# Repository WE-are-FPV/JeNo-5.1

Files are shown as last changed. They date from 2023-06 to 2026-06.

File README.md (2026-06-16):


> [!NOTE]
> Current version : **1.6.0** (read [changelog](#changelog) for details)

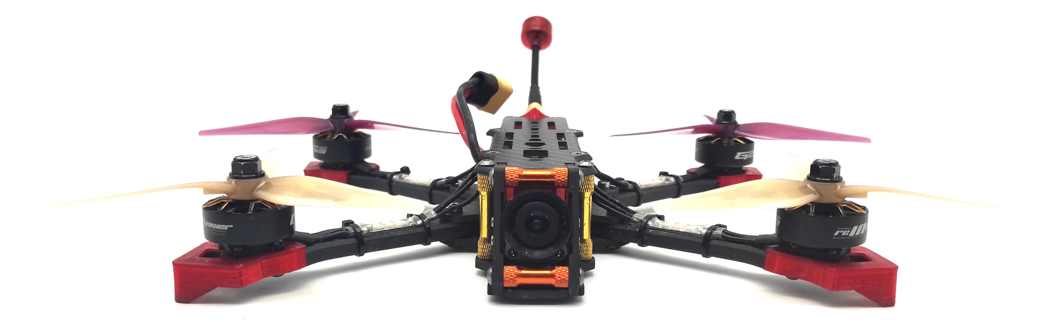
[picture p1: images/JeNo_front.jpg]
JeNo - Front view


# JeNo 5.1"
***5.1" drone FPV frame compatible with Air Unit O3 and O4 Pro, designed for Freestyle, Freeride and Cinematic. Many customizable options are available.***

> [!NOTE]
> Designed in France by members of the [WE are FPV](https://www.wearefpv.fr/) community, the JeNo is already flown by hundreds of pilots and is now being sold by [Drone FPV Racer](https://www.drone-fpv-racer.com/recherche?controller=search&s=JeNo+5.1+frame&aff=64&id_campaign=13) (affiliate link). The French version of the project is available on [Printables](https://www.printables.com/fr/model/339099-jeno-51-drone-frame). Note that a [2.5" version](https://github.com/WE-are-FPV/JeNo-Pocket), [3-3.5" version](https://github.com/WE-are-FPV/JeNo-3-3.5) and a [7-8" version](https://github.com/WE-are-FPV/JeNo-7) of the JeNo exist.

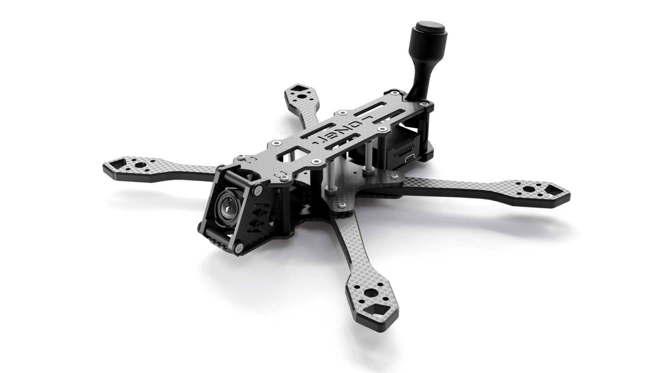
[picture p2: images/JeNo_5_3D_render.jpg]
JeNo classic - 3D render


## Table of contents

* [Key features](#key-features)
* [Presentation](#presentation)
* [Detailed specifications](#detailed-specifications)
* [Versions and files](#versions-and-files)
* [Customization](#customization)
* [Buy it or cut it !](#buy-it-or-cut-it-)
* [Bill of materials](#bill-of-materials)
* [Building/Assembly guide](#buildingassembly-guide)
* [Inspiration](#inspiration)
* [Tuning, Betaflight Preset](#tuning-betaflight-preset)
* [Blackbox](#blackbox)
* [Videos](#videos)
* [Builds examples](#builds-examples)
* [Authors](#authors)
* [TPU](#tpu)
* [Community (remixes and TPU)](#community-remixes-and-tpu)
* [Changelog](#changelog)

## Key features
- [x] **Sturdiness** and **rigidity** (6 mm arms)
- [x] Excellent flight **performances**, easy to tune
- [x] **Wide-X** geometry
- [x] Perfect DJI **Air Unit O3 O4 Pro** camera integration
- [x] Designed for : DJI Vista/AU O3/AU O4 Pro, WalkSnail, HDZero, Analogic
- [x] **Frame and standoffs NOT visible** in video feed, with any FPV camera
- [x] Stack **decoupled** from the arms
- [x] **Easy maintenance** : remove 2 screws to replace an arm
- [x] **Roomy** (30 mm high)
- [x] **Customizable** (weight, arms, camera plates)

## Presentation
The **JeNo** is a 5.1" frame designed for the **DJI Air Unit O3**, which is not compatible with most of existing frames. It was designed to ensure that the frame is not visible in the camera's field of view (FOV) while providing good lens protection. It is also compatible with the O3 camera's ND filters.

The JeNo is now compatible with the **JI Air Unit O4 Pro** (but make sure to use vertical ND filters, like [those from GEPRC](https://geprc.com/product/geprc-dji-o4-air-unit-pro-filter/)).

Originally intended for freestyle flying, **flight quality** and **durability** were at the core of its design (see BlackBox at the bottom of the page).

The issue of obstructed FOV due to standoffs or the frame itself is exacerbated with the O3/O4 Pro camera, but this issue already exists in many frames with other cameras. The JeNo allows for a clear FOV **with any camera** and is **not exclusively dedicated to the O3/O4 Pro**.

It is optimized for a 25° camera tilt but can support FOVs ranging from 0° to ~40°. A high tilt option is also available.

This new ability to film in **4K without needing an Action Cam** saves between 70g (Action 2) and 165g (GoPro 11) (plus TPU). For the standard version of the JeNo, we decided to add 20g to the frame to have a **rigid and sturdy tank**, totaling up to **~140g**. However, it still allows for the option of carrying an Action Cam.

A set of **[optimized TPU for bando bashing](https://github.com/WE-are-FPV/JeNo-5.1/tree/main/tpu/bando_edition)** is also available to guarantee the best durability.

With a DJI Air Unit O3/O4 Pro, you benefit from a **lighter and more robust** setup compared to traditional frames, with a clear FOV.

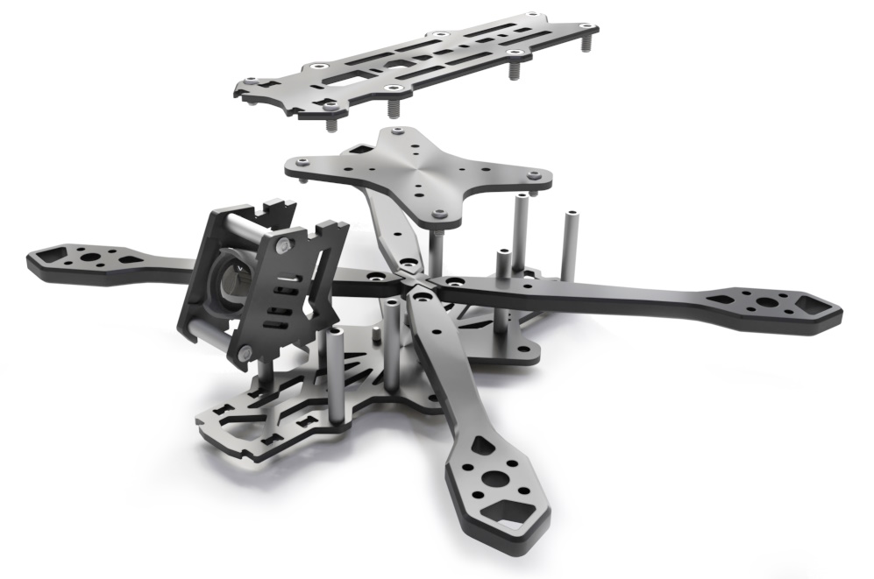
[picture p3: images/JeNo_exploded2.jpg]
JeNo - exploded view


A **Light version** will allow you to maintain a more typical weight around **120g**.

The JeNo was initially designed for Freestyle flying, which is why it features a "Wide-X" geometry. This design allows for good handling while reducing the amount of **visible propellers in the FOV** compared to a "True-X" frame (though some propellers may still be visible). A **"Cinematic" option** provides **elongated camera plates** for a **"Wide" FOV without visible propellers**.

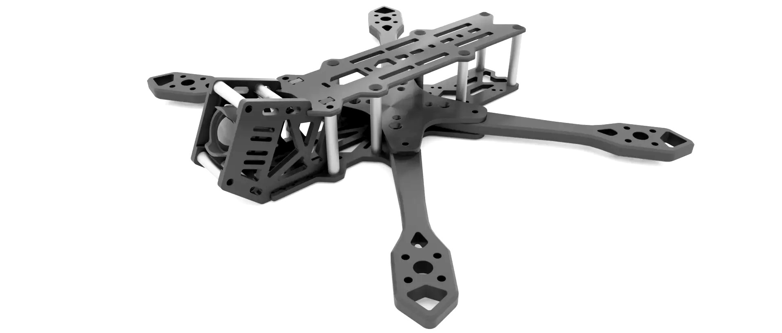
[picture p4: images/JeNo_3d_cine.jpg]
JeNo Cinematic - 3D render


Several pattern options for the arm are also available.

Finally, as this frame was designed by members of the [WE are FPV](https://www.wearefpv.fr/) community, a "WaF edition" is available (the logo is engraved on the bottom plate, you can remove it if you prefer). Join us on the WAF forum in [the official JeNo 5.1" thread](https://forum.wearefpv.fr/topic/19574-jeno-51-un-ch%C3%A2ssis-custom-modulaire-avec-fov-d%C3%A9gag%C3%A9-o3) to discuss it further.

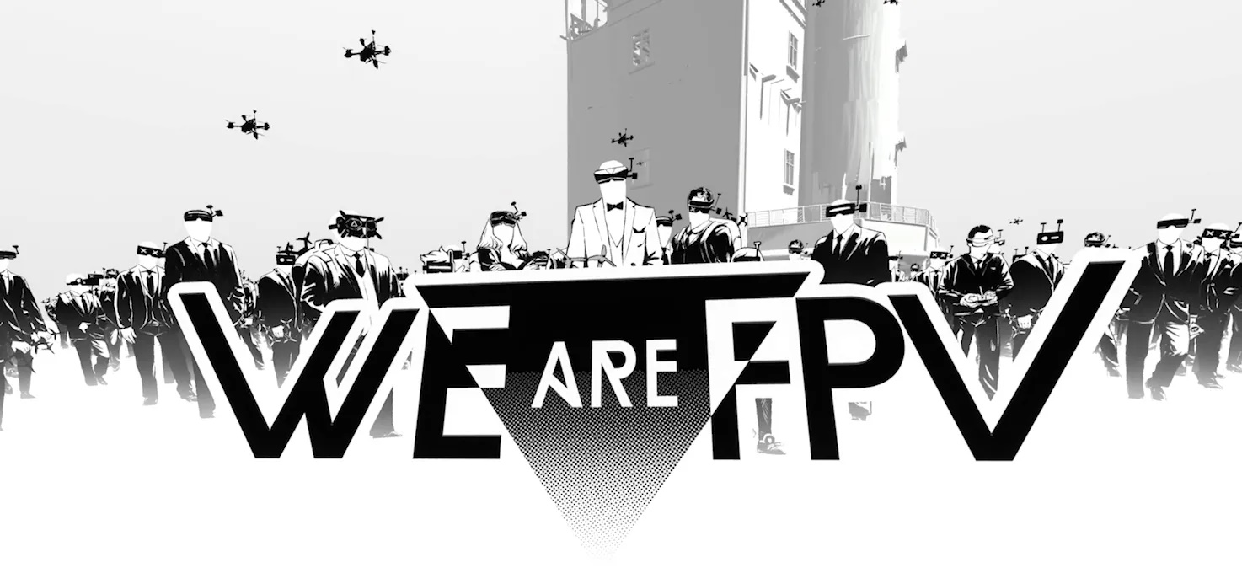
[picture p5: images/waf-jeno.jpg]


The JeNo is also available in [2.5" version](https://github.com/WE-are-FPV/JeNo-Pocket), [3" and 3.5" versions](https://github.com/WE-are-FPV/JeNo-3-3.5) and [7" and 8" version](https://github.com/WE-are-FPV/JeNo-7).

## Detailed specifications

||| 
| :--- | :--- |
| **Geometry** | Wide-X | 
| **Props size** | 5.1" (or 6" with optional arms) | 
| **Weight** | 120 to 145 g depending on options, with screws | 
| **Arms** | 6 mm | 
| **Body height** | 30 mm | 
| **Stack height** | 21.5 mm | 
| **Bottom plate** | 2.5 or 3 mm depending on options | 
| **Middle plate** | 2.5 mm | 
| **Top plate** | 2 mm | 
| **Camera plates** | 3 mm | 
| **Motors mounting** | 16 mm | 
| **Camera** | 20 mm (DJI), Micro, Nano. Clear FOV. Ajustable.
| **Main stack** | 30.5 mm x 30.5 mm and 20 mm x 20 mm | 
| **Back stack** | 20 mm x 20 mm and 25 .5 x 25.5 mm | 
| **Supported VTX** | Analogic, DJI Vista, DJI Air Unit O3/O4 Pro, WalkSnail, HDZero… | 
| **Strap passage** | Yes | 
| **XT60 passage** | Yes (front and back) + passage for a zip tie | 

## Versions and files

### Frame versioning
You will find the **current version** of the frame at the beginning of the description and the full [history of modifications](#changelog) at the end of the page.

We strongly recommend always cutting the latest version to ensure you benefit from the most recent optimizations.

The version **number format** is as follows :
```
<Major versions>.<Minor version>.<Revision>
ex : 1.3.2
```

* **Revision :** This number is incremented in the case of minor modifications with no significant impact.
* **Minor version :** This number is incremented for minor modifications that may potentially break compatibility with certain TPU parts.
* **Major version :** This number is incremented for significant modifications that break compatibility at the carbon level.

Since the creation of the JeNo 5", we have always strived to **maintain compatibility at the carbon level**. As a result, the version remains “1.x.y.”

In practical terms, this means that if you have the very first version of the JeNo 5" and want to equip it with the **O4 Pro**, you only need to have new camera plates cut—they will be compatible with your frame version!

### TPU Versioning

Since TPU parts are tied to the **frame version**, as explained in the previous section, TPU **names are prefixed** with chassis version **compatibility information**, for example :

* JeNo5_**1.6** : compatible with version **1.6**
* JeNo5_**1.x** : compatible with **all** versions
* JeNo5_**1.5+** : compatible starting from version **1.5**

**Note :** if you are developing TPU parts for the JeNo, make sure to clearly indicate which frame version they are compatible with.

### Files management
To simplify things, we have reorganized the file structure. The files are now divided into **five groups** :

* **01-FRAME :** Contains **models** describing the **frame** in DXF, STEP, and STL formats for the current version. Also contains a PDF file which is a reformatted version of the DXF.
* **02-TPU :** Contains **TPU models** for the current frame version in STL format.
* **03-FRAME-HISTORY :** Contains previous versions of the frame.
* **04-TPU-HISTORY :** Contains TPU models that are no longer compatible with the current version.
* **OTHER-FILES :** Contains documentation files, including the assembly manual and a description.

The major change is that all options are now consolidated into a single file. This will make version management significantly easier for us.

If you want to view the DXF file with all annotations, we recommend using the free software [DWG TrueView](https://www.autodesk.com/products/dwg-trueview/overview). If you prefer not to use it, the PDF version of the file will contain all the necessary information.

## Customization

The JeNo is customizable, offering several **options** to best adapt to different needs and individual preferences.

To have a complete frame, you will need to choose:

* A **base** (bottom, middle, top plate, and arm spacer)
* A type of **camera plates**
* A model of **arms**

> [!TIP]
> All components are compatible with each other.

Here is a preview of the "menu card" and its various options:

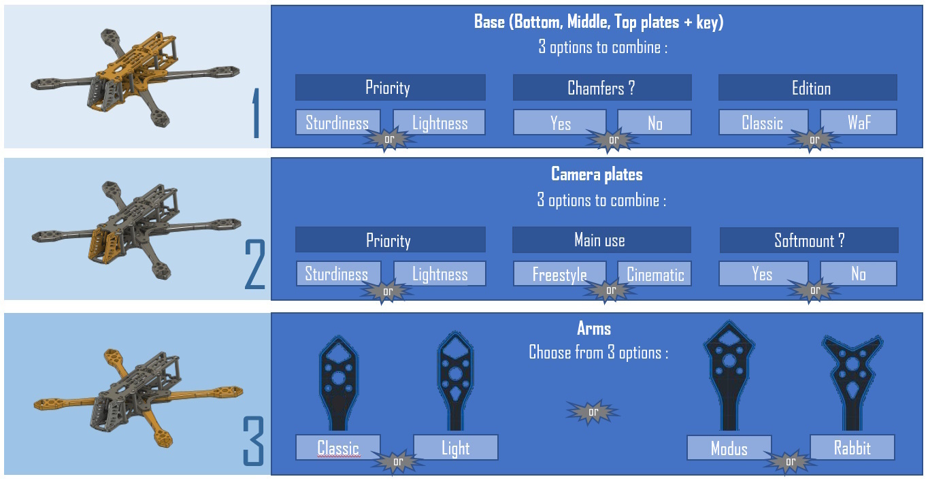
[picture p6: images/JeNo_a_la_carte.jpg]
JeNo customizable options


### The Base
This concerns the core of the frame (bottom, middle, top plates, and arms key).

* **Priority :** The Classic version (sturdy) features a 2.5mm bottom plate, compared to 2mm for the Lightweight version, which is also more "patterned." For the Lightweight version, the weight is approximately 120g depending on the options, compared to approximately 140g for the reinforced (classic) version.
* **Chamfers :** Chamfers have been removed from the files as they are not used by carbon cutters. We recommend applying chamfers to the entire frame, except for the camera plates, for aesthetics, comfort, and durability. Chamfering generally increases the price by around 15%.
* **Edition :** The WE are FPV option adds a "WaF" logo engraved under the bottom plate. You are free to have it removed during cutting or replaced with another design.
* **Bando :** t is the most robust option, with a 3mm thick bottom plate and reinforced arms.

### The Camera Plates

_**Priority :** In the Lightweight version, the carbon is more "patterned," making it slightly more fragile._

* **Classic :** For Freestyle flying, behavior and robustness are prioritized, but the **propellers will be visible in the FOV**.
* **Lightweight :** 2.7g lighter than the Classic plates (1.35g per plate).
* **Cine :** Uses elongated camera plates to remove propellers from the FOV (set to Wide with the O3).
* **Ciné Soft :** The version without soft mounting allows for more adjustment of the camera position. In the case of using the Air Unit O3, the quad must be properly tuned to avoid vibrations in video recording. The soft mounting version limits vibrations that could reach the camera. However we had no vibration with hard mounted O3.
* **High tilt :** allows for a 40° tilt for high tilt adepts
* _**Variable tilt :** variation proposed on [Kamarad70's Thingiverse page](https://www.thingiverse.com/kamarad70/designs)_

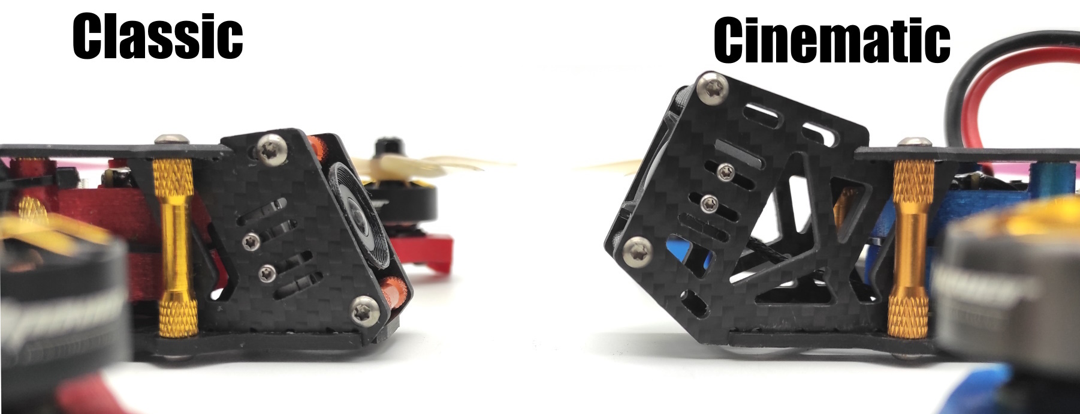
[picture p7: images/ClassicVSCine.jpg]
JeNo Classic vs Cinematic


> [!CAUTION]
> Note: The coaxial cable sold with the Air Unit O3 (11.5 cm) barely fits with the cinematic camera plates. It is recommended to use a 20 cm coaxial cable (sold by RunCam and AxisFlying).
>
> Air Unit O4 Pro coaxial cable is long enough.

| Freestyle camera plates | Cinematic camera plates |
| :---: | :---: |
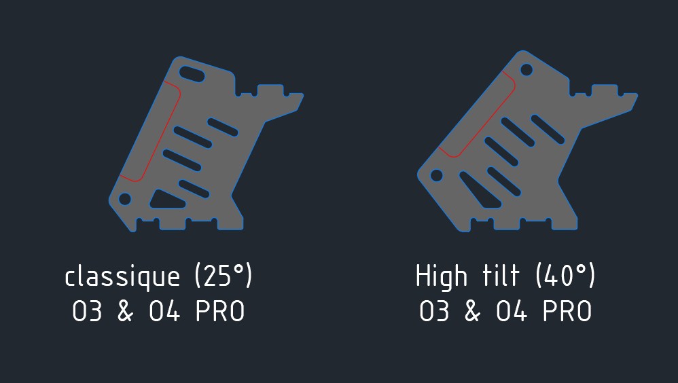
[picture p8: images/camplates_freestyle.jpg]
Freestyle camera plates
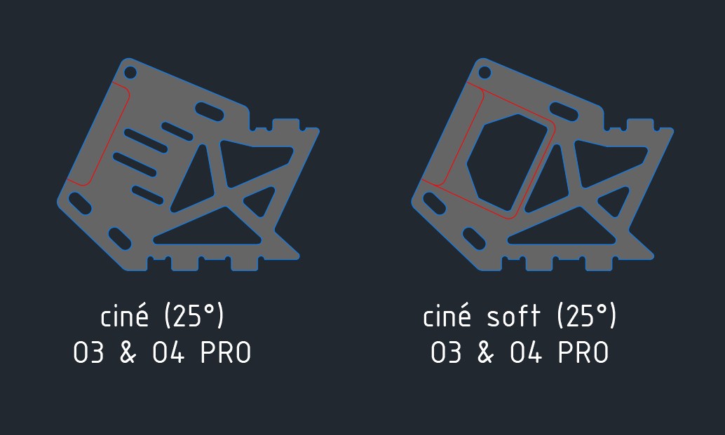
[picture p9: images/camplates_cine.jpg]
Cinematic camera plates
|  |  |
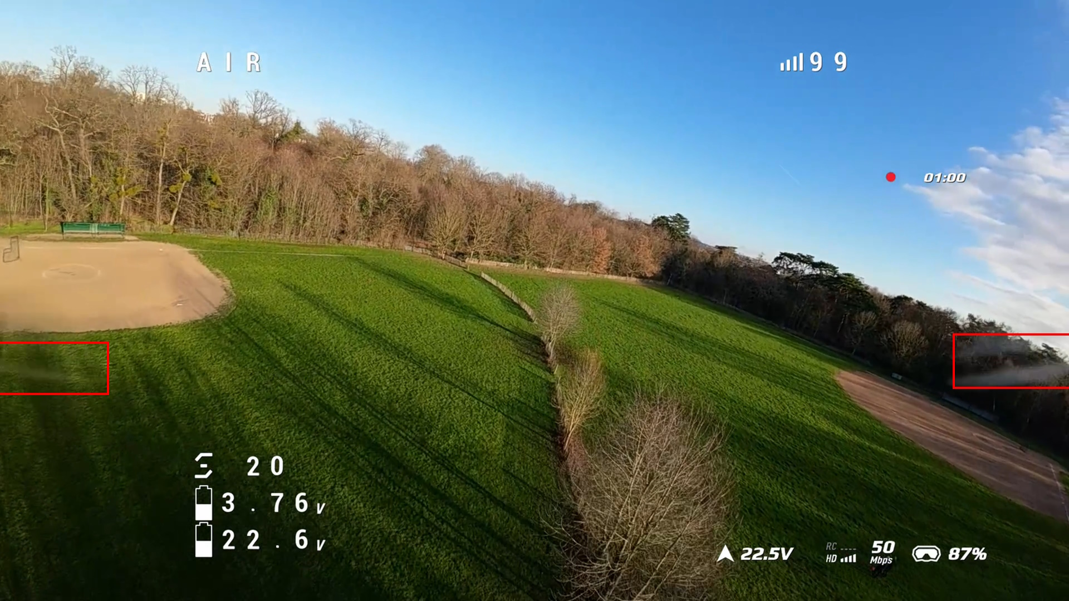
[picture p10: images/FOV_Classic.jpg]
Freestyle Props in FOV
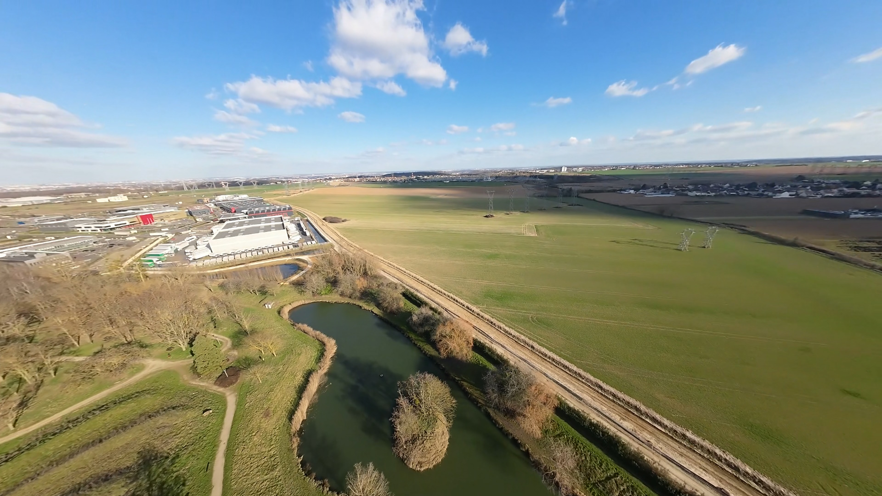
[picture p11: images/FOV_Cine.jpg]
Cinematic No Props in FOV
|  Props in view |  NO props in view |

### The Arms
Several shapes are available for the arm. Weight, robustness, motor protection, and aesthetics will be the main considerations.

* **"Classic" :** A solid design suitable for Freestyle flying.
* **"Light" :** Some solidity is traded in favor of reduced weight.
* **"Modus" :** The most robust shape that offers the best motor protection. It is also the heaviest arm model.
* **"Rabbit" :** Provides good motor protection with a reasonable weight.
* **"Bando Edition" :** A beefier and stronger model

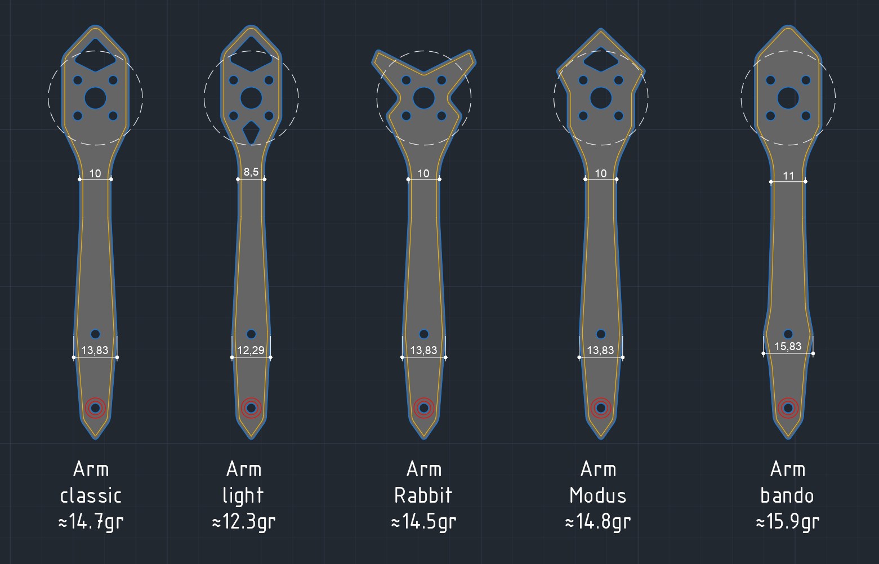
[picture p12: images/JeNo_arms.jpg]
JeNo Arms


### The Extras
In the DXF file, you will find additional options. These "extras" cater to more specific needs but remain compatible with the JeNo :

* 6" Arms
* Ultra-light Camera Plates
* High Tilt Camera Plates (40°)
* Top plate with 2 or 3 straps areas
* ...

Feel free to modify the files according to your requirements as well. For example, if you want even more solidity, you can indicate that you would like thicker bottom and top plates (remember to adjust the screw length accordingly).

A 3mm bottom plate for use in bando is an interesting optimization and does not affect the screws length.

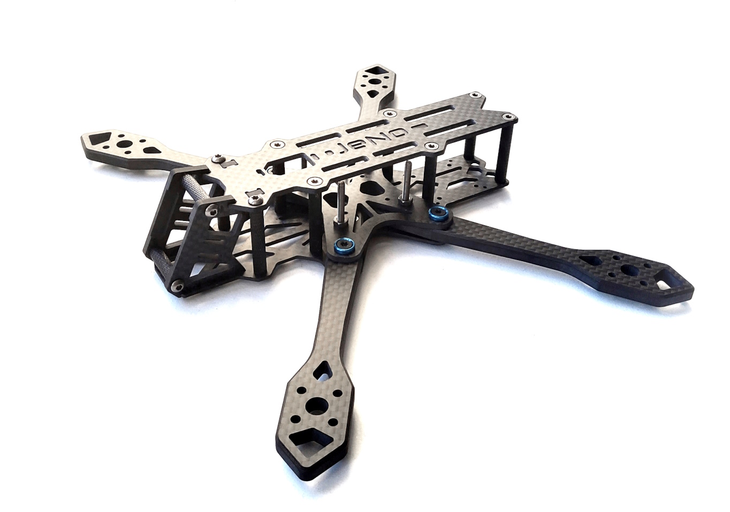
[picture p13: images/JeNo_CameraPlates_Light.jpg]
||
|:---:|
| Classic Base Light + Light Camera Plates + Classic Arms |

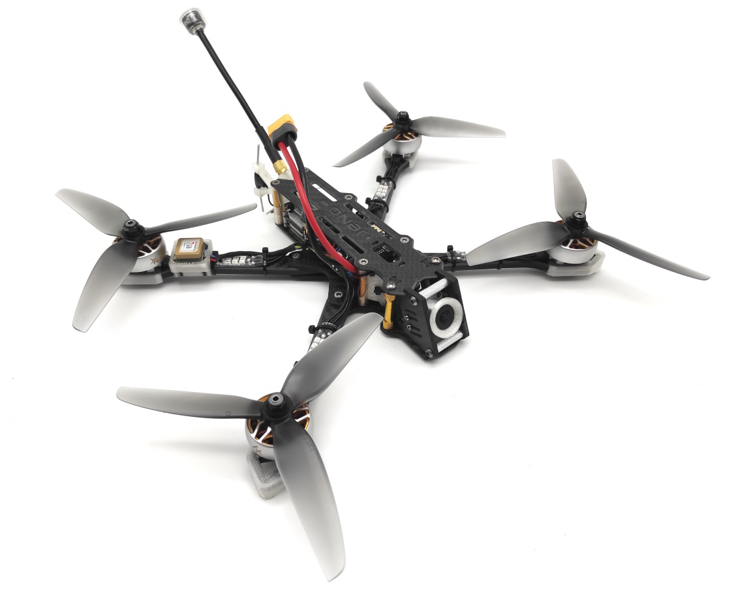
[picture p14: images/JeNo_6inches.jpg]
||
|:---:|
| JeNo Classic + 6" Arms |

## Buy it or cut it !

It is up to you : you can get it cut or you can get a classic or cine version directly from Drone FPV Racer or La Camera Embarquée :

* [JeNo Classic by DFR](https://waf.link/JeNo-DFR) (affiliate link)
* [JeNo Cine by DFR](https://waf.link/JeNo-Cine-DFR) (affiliate link)
* [JeNo Classic by La Caméra Embarquée](https://www.lacameraembarquee.fr/we-are-fpv/17793-chassis-we-are-fpv-jeno-51-classic.html) (affiliate link)
* [JeNo Cine by La Caméra Embarquée](https://www.lacameraembarquee.fr/we-are-fpv/17789-chassis-we-are-fpv-jeno-51-cine.html) (affiliate link)
* [FPV CNC Drone](https://fpvcncdrone.com/)

Note: Prices are often excellent in stores, but they don’t always offer the latest version.

The JeNo 5.1" is also available from [CNC Madness](https://cncdrones.com/jeno-5-classic.html) (Canada).

Of course, you can directly contact your favourite carbon fiber cutting service.

The ["01-FRAME"](https://github.com/WE-are-FPV/JeNo-5.1/tree/main/01-FRAME) folder contains all the files you need to get it **cut** in your favourite flavour.

Consult the **DXF file** of the frame (or the PDF version) to choose the version that interests you.

Feel free to select a pre-made "Edition" (Classic, Light, or Bando), or mix different options and choose certain "extras".

You will also need to choose a type of camera plates (classic, cine, etc.).

> [!NOTE]
> All parts versions are compatible with each others

## Bill of materials

In addition to the carbon fiber, you will need the following hardware to complete the assembly of the frame.

**Standoffs**

It is recommended to use 5mm diameter standoffs, especially for those that will serve as support for TPU (backpack and capacitor). Moletted spacers can still be used, but the TPU supports will need to be modified accordingly.

| Quantity | Description | Details |
| :---: | :--- | :--- |
| 8 | M3x30mm standoffs | for the body |
| 2 | M3x20mm standoffs | for the camera |

**Stack materials**

* If 30x30 stack

| Quantity | Description | Details |
| :---: | :--- | :--- |
| 4 | M3x22mm ou M3x20mm countersunk screws | for the stack |
| 4 | M3 nuts for stack screws | |

* If 20x20 stack

| Quantity | Description | Details |
| :---: | :--- | :--- |
| 4 | M2x20mm countersunk screws | for the stack |
| 4 | M2 nuts for stack screws | |

**Frame materials**

| Quantity | Description | Details |
| :---: | :--- | :--- |
| 6 | M3x6/8mm countersunk screws | for the top plate |
| 14 | M3x8mm screws (titanium if possible) | for the bottom and camera plates |
| 8 | Pressnuts ([Flywoo](https://www.drone-fpv-racer.com/flywoo-m3-clinch-nuts-20-pcs-7965.html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) or SourceOne alike) | |
| 4 | M3x14mm screws (steel if possible) | for the arms |
| 4 | M3x8mm screws (steel if possible) | for the arms |

**Additional materials**

| Quantity | Description | Details |
| :---: | :--- | :--- |
| 16 | M3x10mm screws (if using arms protections) or M3x8mm (if no TPU) | for the motors |
| 4 | M2x5mm screws | for the camera |

_**In the absence of arm protection, 8mm screws are recommended. 10mm screws are sometimes too long for certain motors and can cause current leaks.**_

**Fasten the lipo**

The JeNo allows the use of non-slip straps thanks to its strap slots. You can also use a LiPo pad if desired.

## Building/Assembly guide

Find numerous examples of builds on the _**DroneBuilds**_ page of WE are FPV.
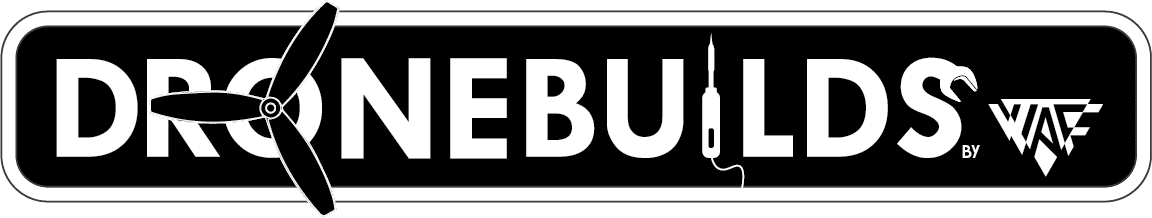
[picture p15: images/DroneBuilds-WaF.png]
DroneBuilds (https://forum.wearefpv.fr/71-dronebuilds/ "DroneBuilds - Click to Access!")


The assembly of the frame is straightforward, but here are some clarifications:

* On one of the two sides of the middle plate, there are chamfered holes to accommodate countersunk screws. This side corresponds to the bottom. Remember to install the stack screws before installing the middle plate.
* The press nuts will be positioned on the bottom side of the bottom plate.
* An RX antenna in the shape of a T can be attached to the back of the JeNo using zip ties.
* Six screws on the top plate are countersunk screws to avoid damaging the LiPo battery.

Here is a [video of the JeNo assembly (FR)](https://youtu.be/SF4UAqyNPJ0), and you will find the assembly documentation below, also available here in [PDF format](./OTHER-FILES/JeNo5_Assembly_Guide.pdf).

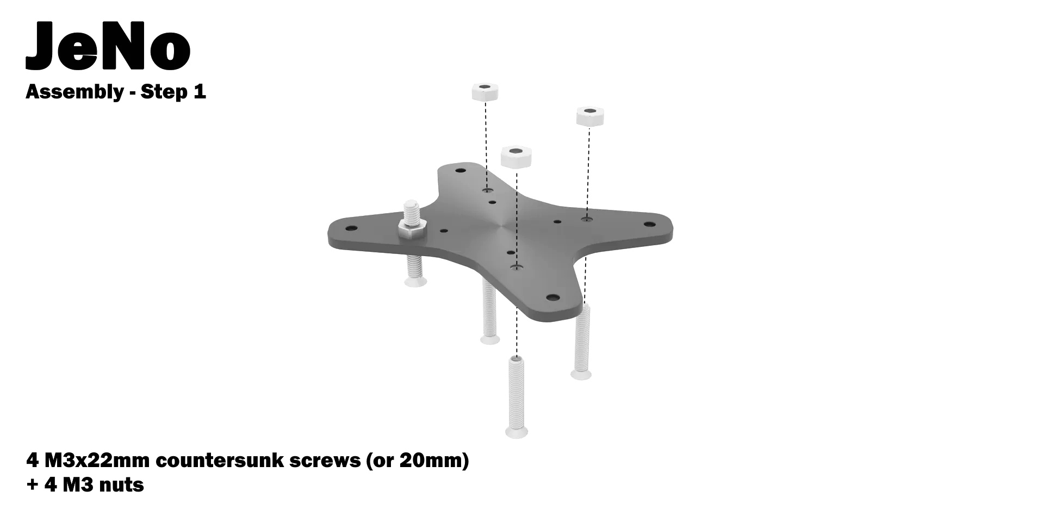
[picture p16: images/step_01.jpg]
JeNo assembly - step 1

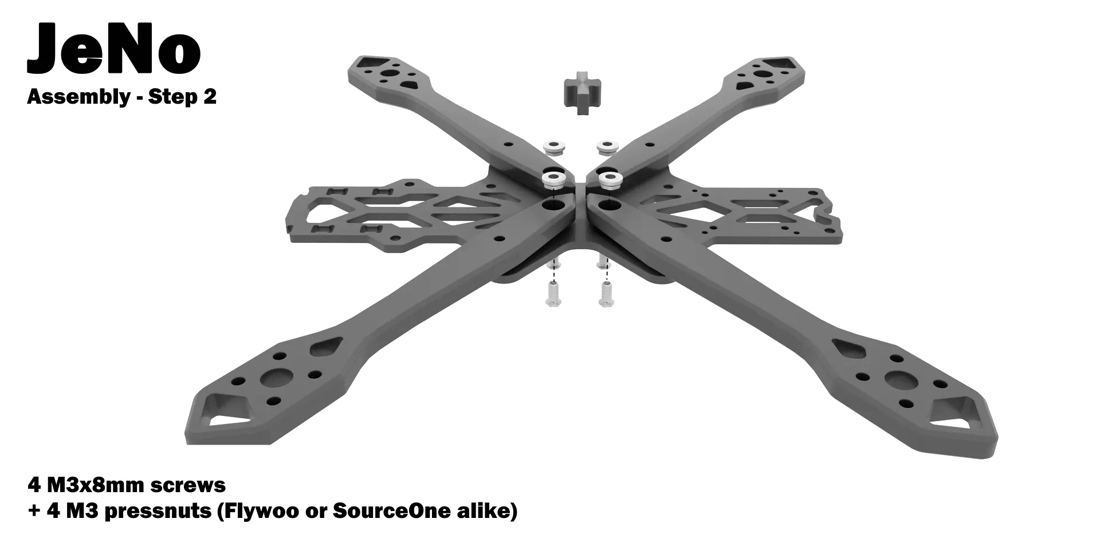
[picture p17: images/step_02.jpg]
JeNo assembly - step 2

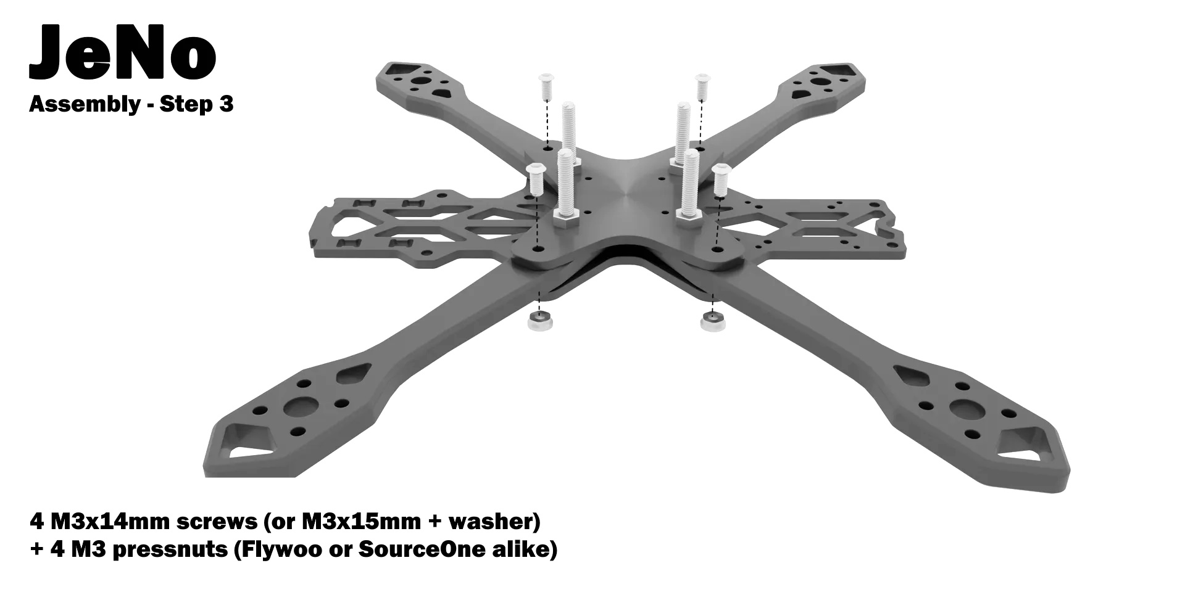
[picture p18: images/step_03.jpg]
JeNo assembly - step 3

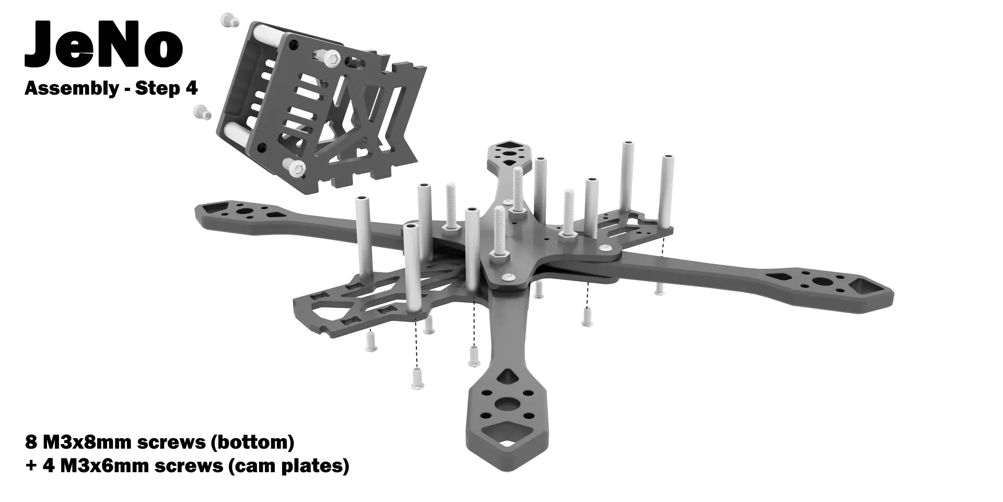
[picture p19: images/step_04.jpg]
JeNo assembly - step 4


The assembly is illustrated with cinematic camera plates, which allow the use of up to 4 standoffs (see visual in step 5 below). In practice, 2 standoffs at the front are sufficient, just like with regular camera plates (see step 4).

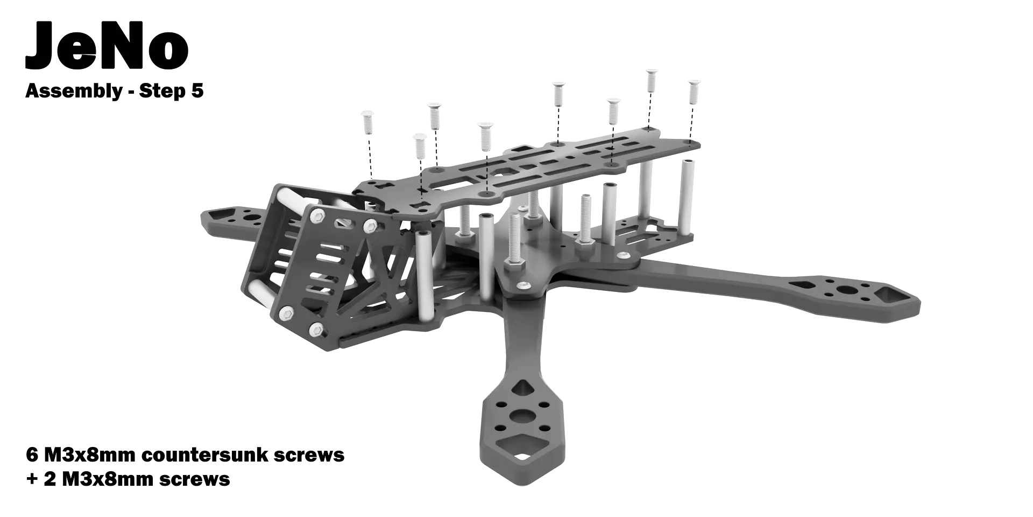
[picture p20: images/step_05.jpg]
JeNo assembly - step 5

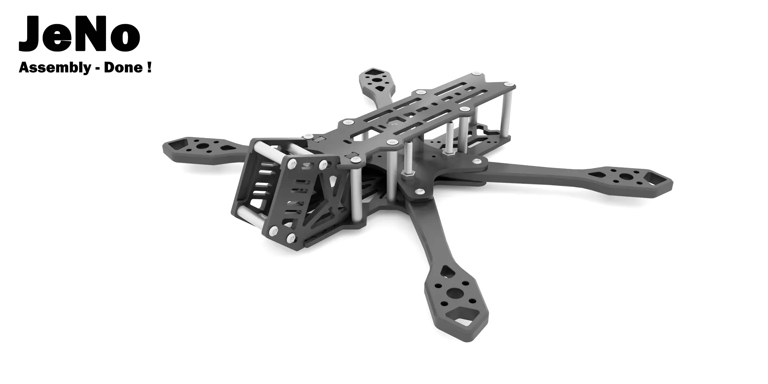
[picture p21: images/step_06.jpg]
JeNo assembly - step 6


## Inspiration

The JeNo takes partial inspiration from two other frames:

* The arm locking system of the **Apex**, with **embedded press nuts** at the end of the arms.
* The camera plates are slightly inspired by the **aluminum** cage of the **iFlight Evoque F5X HD V2**. The design is completely different as we use only carbon fiber, but the look is similar.

The rest of the design was guided by the constraints imposed by the Air Unit O3 and its camera, as well as our past experiences with other custom frame designs.

## Tuning, Betaflight Preset

To quickly and fully enjoy the JeNo, a **preset** for **Betaflight 4.4 and 4.5** is available. You just need to add the **WE are FPV repository** to the **preset sources** in Betaflight Configurator.

In the "Preset" tab, click on "Preset sources..." to add the WE are FPV source:

- **Url :** https://github.com/WE-are-FPV/firmware-presets
- **GitHub branch :** waf-presets

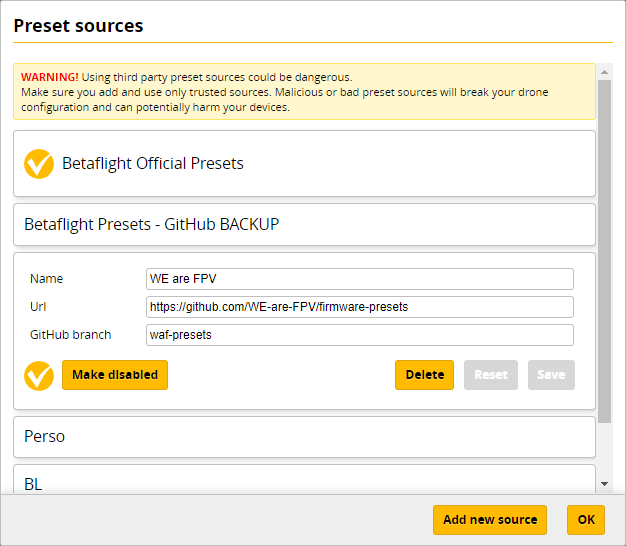
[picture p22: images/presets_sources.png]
JeNo Preset Source


Once the source is validated, you simply need to make it "active" to access the JeNo presets under the **"Tune" category** in **version "4.4 or 4.5"**. The preset is available in both **French (FR)** and **English**, and it is indeed the **same tune**.

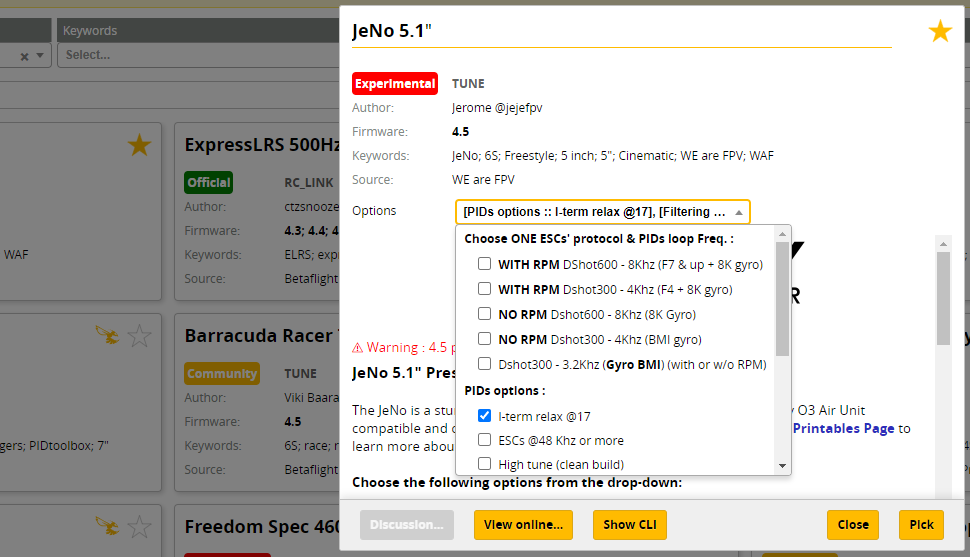
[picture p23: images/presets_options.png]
JeNo Preset Options


The preset contains **several options** to select. Note that **by default**, the **tune** is already **quite aggressive**, even without activating the "advanced" tuning options for PIDs and filtering.

## Blackbox

Here is an overview of vibration distribution on the 3 axes for the JeNo "classic Freestyle." This is indeed the unfiltered gyro signal for a 3 minutes freestyle flight :

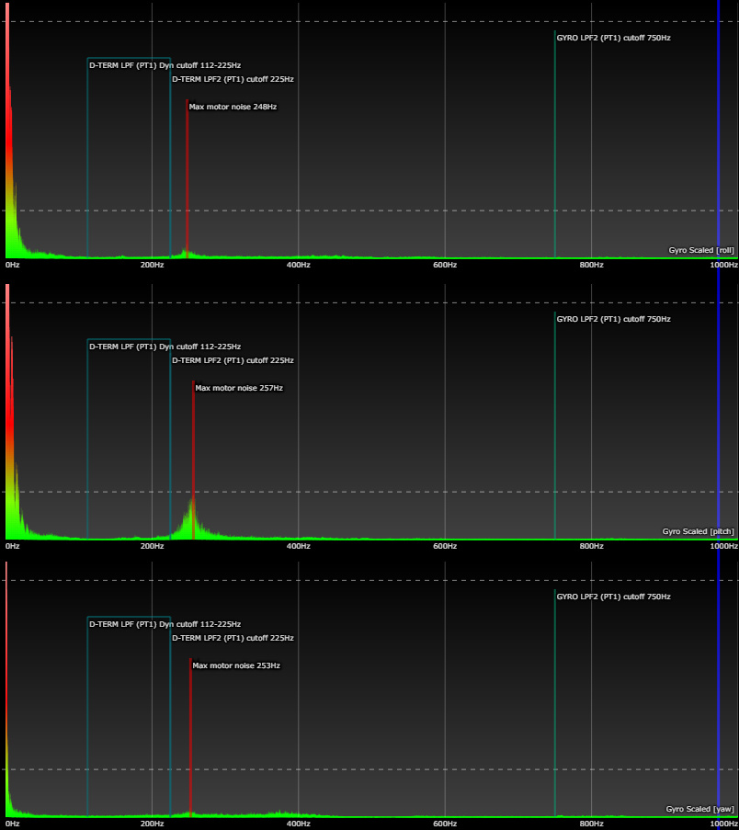
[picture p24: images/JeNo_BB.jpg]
JeNo Blackbox


## Videos
Freestyle with JeNo :

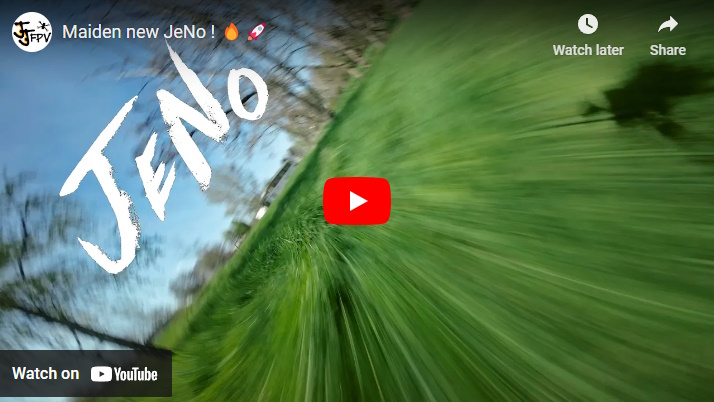
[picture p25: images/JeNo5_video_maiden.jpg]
JeNo 5.1 Maiden (https://www.youtube.com/watch?v=Fe3_sJf0j6o "JeNo 5.1 Maiden - Click to Watch!")


JeNo review on WE are FPV (French) :

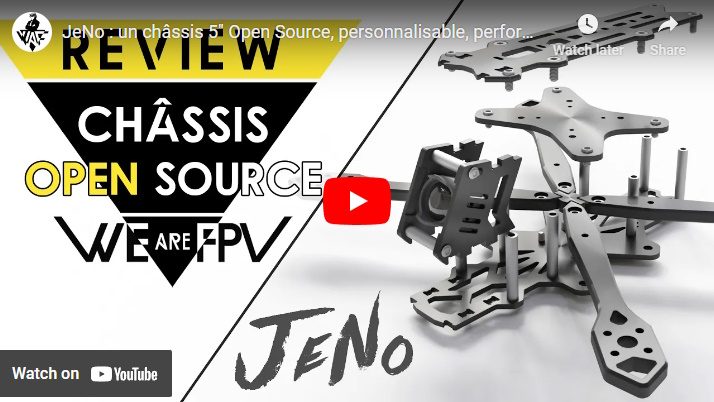
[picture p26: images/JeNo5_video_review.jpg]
JeNo review on WE are FPV (French) (https://www.youtube.com/watch?v=RtPTJsno8Kg "JeNo review on WE are FPV (French) - Click to Watch!")


## Builds examples

You can find many build examples on [WE are FPV's DroneBuilds](https://forum.wearefpv.fr/71-dronebuilds/) and [RotorBuilds](https://rotorbuilds.com) :

* en : [JeNo 5.1" WE are FPV O3](https://rotorbuilds.com/build/31216)
* fr : [Iron JeNo 5.1" (Vista)](https://forum.wearefpv.fr/topic/20347-iron-jeno-51-vista/)
* fr : [JeNo - DJI Air Unit O3 (5" 6S)](https://forum.wearefpv.fr/topic/19543-jeno-dji-air-unit-o3-5-6s/)
* fr : [JeNo 6" cine/midrange](https://forum.wearefpv.fr/topic/20536-jeno-6-cinemidrange/)
* fr : [JeNo 5.1" Hybride](https://forum.wearefpv.fr/topic/20239-jeno-51-hybride/)
* fr : [JeNo 5" Cam Plate Ciné](https://forum.wearefpv.fr/topic/19995-jeno-5-cam-plate-cin%C3%A9)
* ...

## Authors

The JeNo was designed by :

* nochamo - [Youtube](https://www.youtube.com/user/nochamo)
* Jerome / Jéjé FPV - [Youtube](https://www.youtube.com/@jejefpv)
* MotardGeek - [Youtube](https://www.youtube.com/@MotardgeekFr91) (requester and tester for Light version)

## TPU

Among the downloadable files, you will find a variety of TPU to protect your JeNo and different Action Cams.

Even more interestingly, in collaboration with **Alex**, also known as [Heim FPV](https://www.youtube.com/@heim_fpv589), from the **__#bandolovers__** team, we have designed a set of [TPU parts optimized for bando flying](https://github.com/WE-are-FPV/JeNo-5.1/tree/main/tpu/bando_edition). If you're looking to reinforce your JeNo to the maximum extent, this kit is tailored for you. It includes:

* A **front bumper** that will safeguard the entire camera cage and assist in absorbing frontal impacts. It is available for classic, cine and high tilt camera plates.
* A **back bumper** for worry-free matty flips (it also allows for attaching the RX antenna).
* A much sturdier and encompassing **VTX antenna support**, with an inclination that better tolerates impacts from the rear (available in O3 and "cherry" versions). 2 holes allow for an easy antenna ejection if required.
* 2 new **arm protections**, offering not only better arm protection but also motor protection. The first version is "clippable" and replaceable without disassembling the motors. The second completely encases the arm tips and has no chance of being ejected during a crash.
* An optimized **DJI Action 2 mount** for bando flying, without an ND filter, available in 20 and 25-degree versions (not the one on the photo here under, which is the classic version).
* A new **DJI Action 2 mount** remixed from [T4 Max FOV Action 2 DJI TPU Drone Mounts](https://www.printables.com/fr/model/217897-t4-max-fov-action-2-dji-tpu-drone-mounts) par [t4obrien](https://www.printables.com/fr/@t4obrien). It allows to secure the camera with a strap.

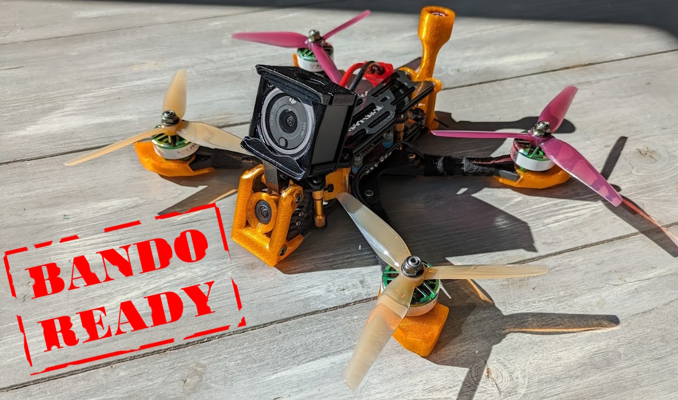
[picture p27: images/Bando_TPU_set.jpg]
Bando TPU set


If the cap of your Air Unit O3 antenna is lost, several designs are [available here](https://www.printables.com/fr/model/556697-dji-air-unit-o3-antenna-cap-3-versions) for replacement.

## Community (remixes and TPU)

**Fork/remix**
* [Platy FPV](https://www.youtube.com/channel/UCqOLDBE34WiqytAgCRManAg) has reimagined the JeNo to suit his needs: lighter, shorter, low profile, and with a split deck. Find all the details of the [JeNo 5.1" - PlatyStyle Edition](https://www.printables.com/fr/model/744619-jeno-51-platystyle-edition) on their Printables page and on the [WE are FPV forum](https://forum.wearefpv.fr/topic/22236-jeno-51-platystyle-un-jeno-sous-hormones).

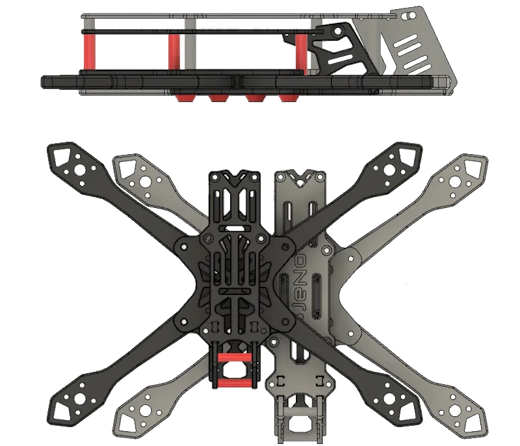
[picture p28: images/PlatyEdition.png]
PlatyStyle Edition


* [Kamarad70 (Rotor-Vision)](https://www.youtube.com/channel/UCQ9MUpBuCL820obqPXN7wsw) offers a variation of the JeNo camera plates on [his Thingiverse page](https://www.thingiverse.com/kamarad70/designs), allowing for an adjustable tilt (from -20° to approximately +40°). You will also find the associated [FPV camera mount](https://www.thingiverse.com/thing:6627268), a [front bumper](https://www.thingiverse.com/thing:6627192), and an [Action Cam support base](https://www.thingiverse.com/thing:6627160).

**TPU**

In addition to the TPU options available on this page, you will find here some TPU designs created by the community.

* [Pulse FPV](https://www.youtube.com/channel/UCUWnkQ2-IbQYc6LpTXz01qw) has created an impressive collection of high-quality TPU designs, which can be found on his [Thingiverse page](https://www.thingiverse.com/thing:5804682).

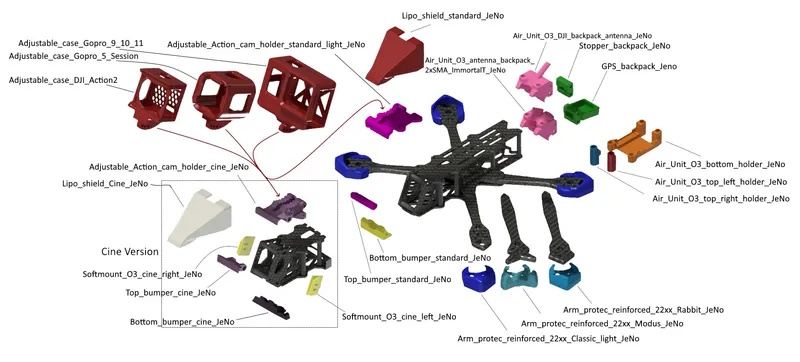
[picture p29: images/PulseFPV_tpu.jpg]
PulseFPV TPU


* [Bard FPV](https://www.youtube.com/@bardfpv) also offers us some interesting TPU designs on their [Cults3D page](https://cults3d.com/fr/collections-de-designs/BardFpv/jeno), including fins to protect the LiPo and facilitate the turtle mode.

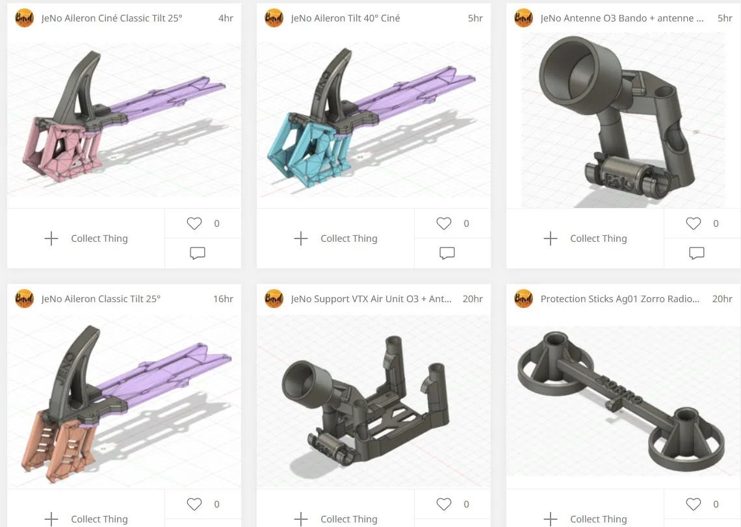
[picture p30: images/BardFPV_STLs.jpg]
Bard FPV STLs


* [Support GP9, Walksnail, GPS, ViFly etc.](https://www.thingiverse.com/-kc-/designs) by [kC](https://www.youtube.com/@kCer)
* [Modus rising arm protection](https://www.printables.com/fr/model/830201-jeno-51-protection-bras-modus) to safeguard the bells, [short double antenna backpack](https://www.printables.com/fr/model/830229-jeno-51-support-double-antennes-vista-pour-o3) by [Florian](https://www.printables.com/fr/@FloG_149541/models). 
* Several [GoPro mounts](https://www.printables.com/fr/@PhenXFrame/models) (5 to 7 and 9 to 12) by [Phen X Frame](https://www.printables.com/fr/@PhenXFrame)
* [GoPro Mini 11 mount](https://www.printables.com/fr/model/831787-jeno-51-gopro-11-mini-mount) and other STL files by [L4go](https://www.printables.com/fr/@L4go_1956352)
* [GoPro Mini 11 mount](https://www.printables.com/fr/model/590286-gopro-11-mini-pour-jeno-cine) for JeNo Cine by [shaks](https://www.printables.com/fr/@shaks_729955)
* [O3 case](https://www.printables.com/model/1032747-jeno-bando-o3-casing-ranxfpv), 2 O3 backpacks with fins ([V1](https://www.printables.com/model/976839-jeno-bando-o3-backpack-ranxfpv) and [V2](https://www.printables.com/model/1032734-jeno-bando-o3-backpack-ranxfpv-v2)) and a [front bumper with fins](https://www.printables.com/model/1032740-jeno-bando-bumper-avant-ranxfpv) by [Franck G](https://www.printables.com/@FranckG_2243891)
* Still by [Franck G](https://www.printables.com/@FranckG_2243891), but for the O4 Pro : DJI O4 Pro casing ([V1](https://www.printables.com/model/1144921-jeno-bando-dji-o4-pro-casing-ranxfpv), [V2](https://www.printables.com/model/1168238-jeno-bando-dji-o4-pro-casing-ranxfpv-v2)), [front bando bumper](https://www.printables.com/model/1158816-jeno-o4-pro-bando-bumper-avant-ranxfpv) and [a linear antennas backpack](https://www.printables.com/model/1146819-jeno-bando-dji-o4-o3-backpack-ranxfpv-v3)

## Changelog

> [!TIP]
> Compatibility is consistently maintained between each version: if your frame was a v1, the parts from v1.2 will be compatible. The same applies to TPU accessories. That's why we don't keep the history of previous versions.

* Version **1.6.0** (13/12/2025) :
  * New bottom plate for all variants : reinforcement of the front section around the camera plate slots
  * New top plate for all variants : widened carbon area around the rear holes to make cutting easier and improve durability
  * **TPU :** new front bumpers to account for the bottom plate modification
  * **TPU :** new backpacks to account for the top plate modification
  * **TPU :** new mounts for the DJI Osmo Nano
  * **Important :** Action Cam mounts are not affected by this update. They were only impacted when O4 Pro support was introduced in version 1.5.1.
  * **Important :** This version update does not break compatibility of the carbon cuts with the previous version.
  * For clarity, TPU filenames are now prefixed with chassis version compatibility information, for example :
    * JeNo5_**1.6** : compatible with version **1.6**
	* JeNo5_**1.x** : compatible with **all** versions
	* JeNo5_**1.5+** : compatible starting from version **1.5**
* 16/09/2025 :
  * New TPU arm and motor bumpers, more optimized and offering even greater protection for the motors.
* 16/02/2025 : 
  * Addition of TPU for softmounted camera plates (works with O3 and O4)
* Version **1.5.1** (01/02/2025) : 
  * Support for the **Air Unit O4 Pro** (camera plates + TPU)
  * Widening of the bottom plate around the Air Unit O4
* 01/10/2024 : 
  * STL "JeNo_arm protect_full_socket_bando" from the TPU bando kit updated to fix errors with some slicers
* Version **1.4.0** (02/09/2024) :
  * Modification of the bottom plate on the Classic versions (strength optimization). The "Light" versions remain unchanged.
  * Addition of TPU bando (front bumper and rear bumper) adapted for a 3mm bottom plate.
  * The STL and STEP files have been updated to accommodate the new bottom plate.
* 19/01/2024 :
  * Betaflight 4.5 JeNo Preset added (on WAF repo)
* Version **1.3.1** (13/12/2023) :
  * Hole removed from classic arms
  * Slight optimization of the bottom plate for increased solidity (classic edition only)
  * 2 straps top plate is the new default for increased solidity (classic edition only)
* 08/10/2023 : 
  * Bando arm added (dans “dxf\03_arms”), with no holes and a bit beefer
* 03/09/2023 : 
  * Collection of reinforced TPU optimized for bando added (in “tpu\bando_edition”)
* 08/07/2023 :
  * New top plate with only 2 straps passages to mitigate a weak point if the front strap passage is not needed (in “dxf\04_extras”)
* 24/04/2023 :
  * High tilt camera plates added (in “dxf\04_extras”)
* 09/03/2023 :
  * 6" arms added (in “dxf\04_extras”)
* Version **1.2.0** (Drone-FPV-Racer) :
  * Modification of the top plate with the engraving "JeNo" (the old top plate is still available in "dxf/04_extras").
  * Addition of chamfers on the top plate (for strap routing, XT-60 pass-through).
  * Reinforcements at the back of the bottom plate.
  * Addition of a chamfer on the bottom plate (single face).
  * Extra-light camera plate on the "light"  version (full and base DXF).

## Join the JeNo family !

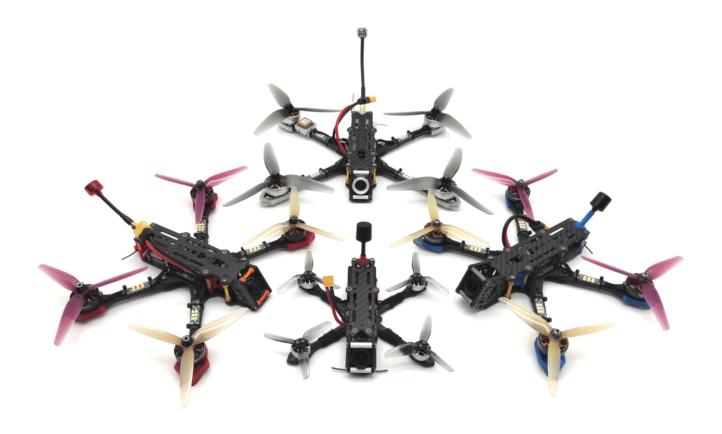
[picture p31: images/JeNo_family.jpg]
||
|:---:|
| JeNo Classic Modus (left), JeNo Cine (right), JeNo 6" (top), JeNo 3" (bottom) |

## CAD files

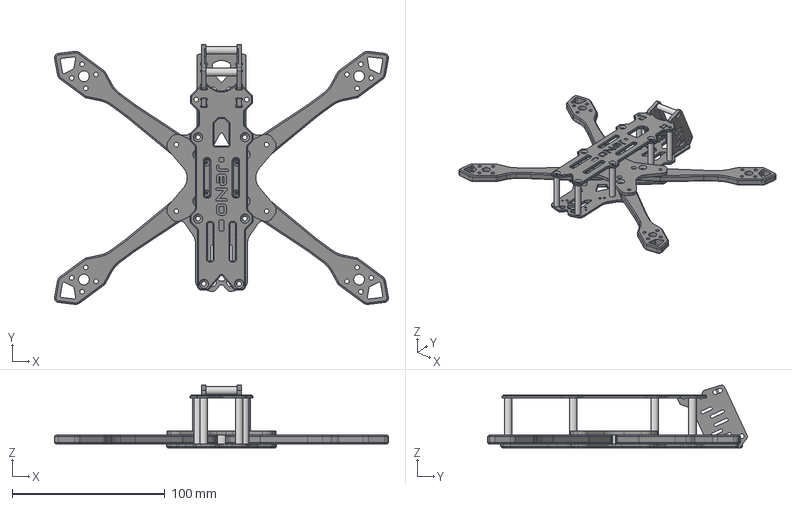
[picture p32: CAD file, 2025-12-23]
01-FRAME/JeNo 5_1.6.0.step
218.5 x 170.0 x 41.1 mm

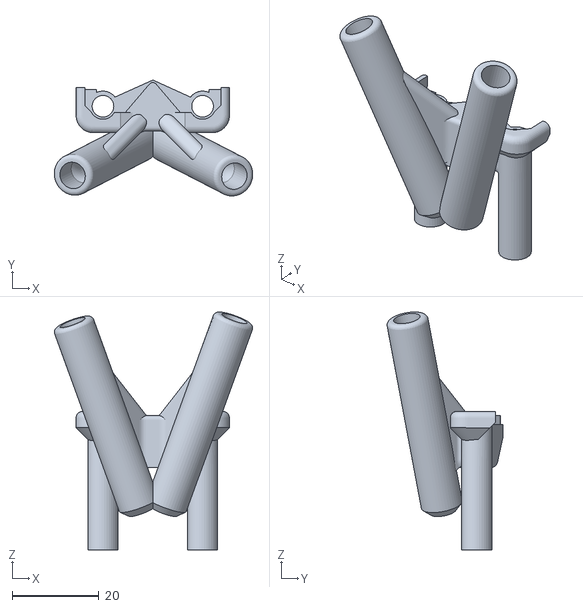
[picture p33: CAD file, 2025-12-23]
02-TPU/JeNo5_1.6_Antennas_DoubleLinear.stl
45.8 x 26.8 x 54.9

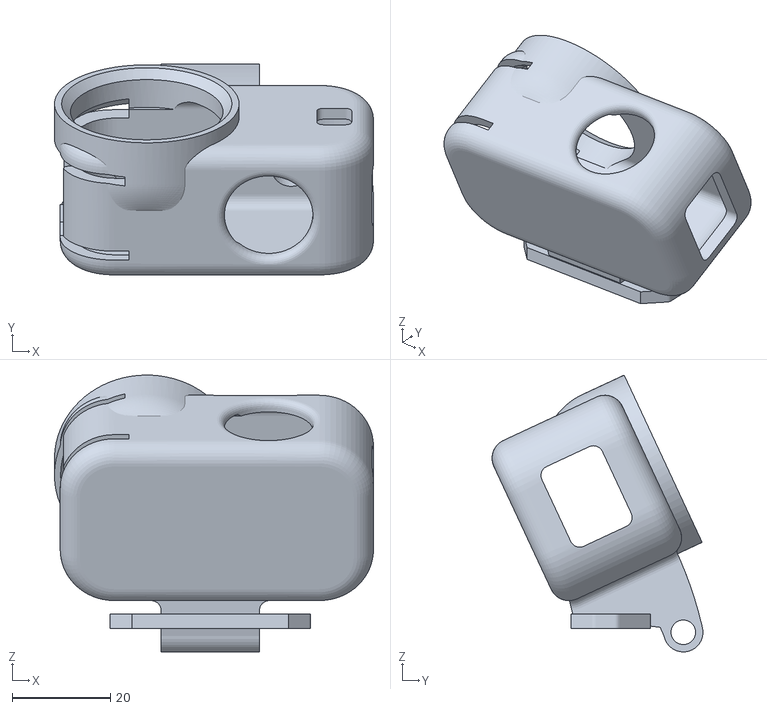
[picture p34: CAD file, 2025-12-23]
04-TPU-HISTORY/jeno5_1.4_support_osmo_nano_25deg.stl
64.8 x 42.9 x 56.3

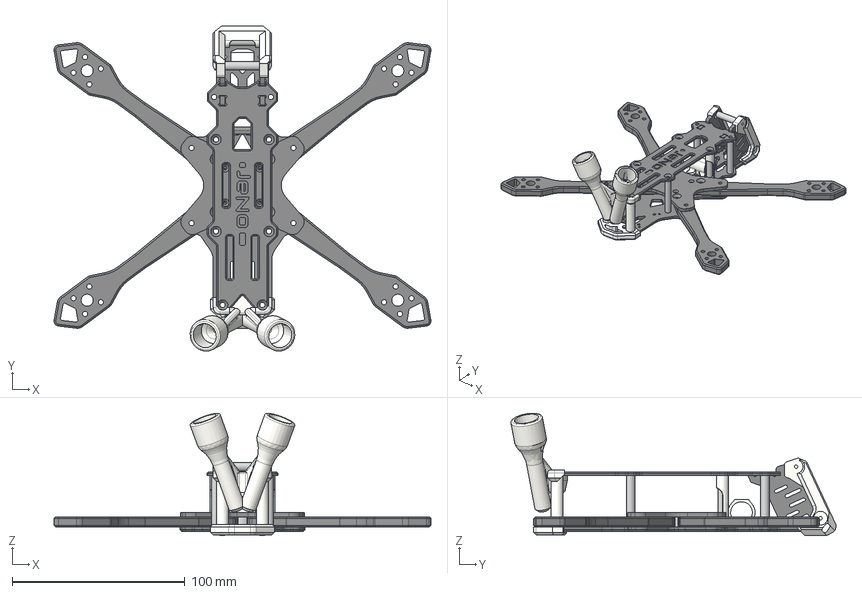
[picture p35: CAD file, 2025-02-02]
03-FRAME-HISTORY/JeNo5_1.5.1_ALL_VERSIONS.step
218.5 x 188.5 x 71.0 mm

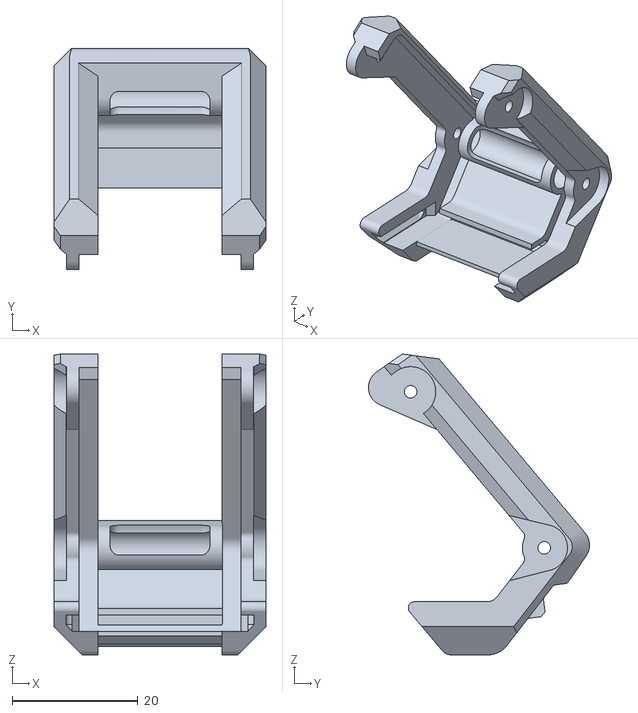
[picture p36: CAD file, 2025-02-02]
04-TPU-HISTORY/JeNo5_1.5.1_Bumper_Front_HighTilt_40.stl.stl
33.8 x 35.2 x 47.9

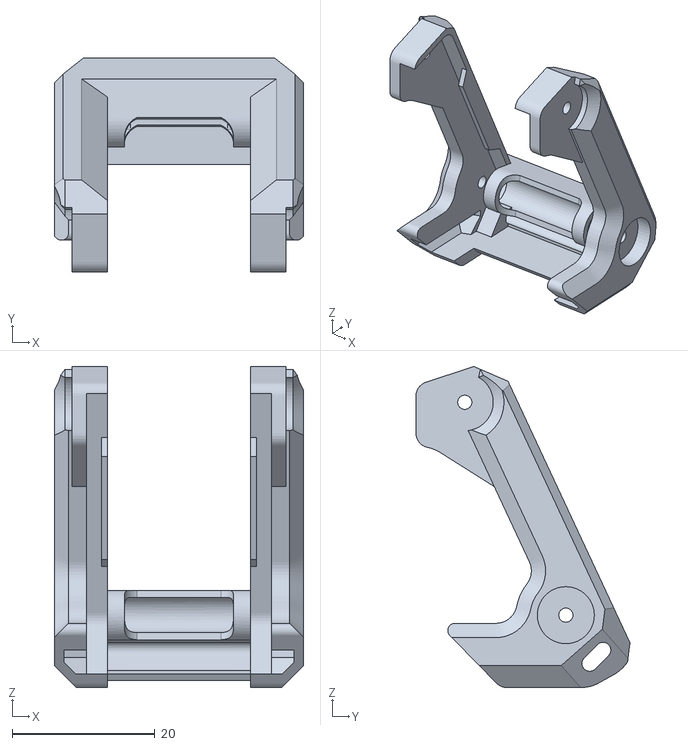
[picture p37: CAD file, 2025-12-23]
02-TPU/JeNo5_1.6_Bumper_Front_25deg _3mm.stl
35.0 x 30.0 x 45.0

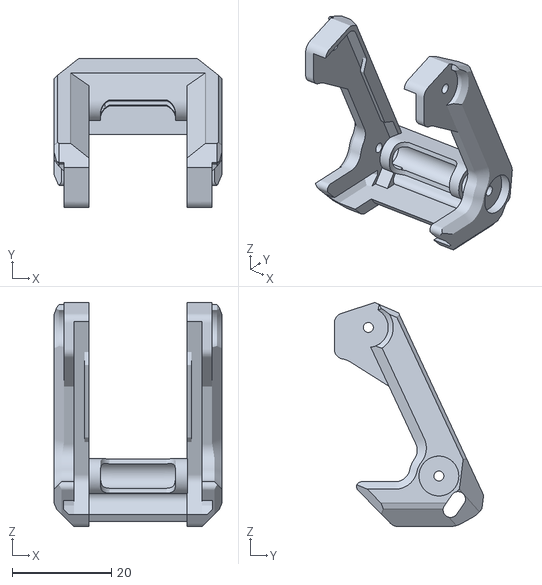
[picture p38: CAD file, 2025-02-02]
04-TPU-HISTORY/JeNo5_1.5.1_Bumper_Front_Classic_25.stl
33.8 x 30.0 x 45.0

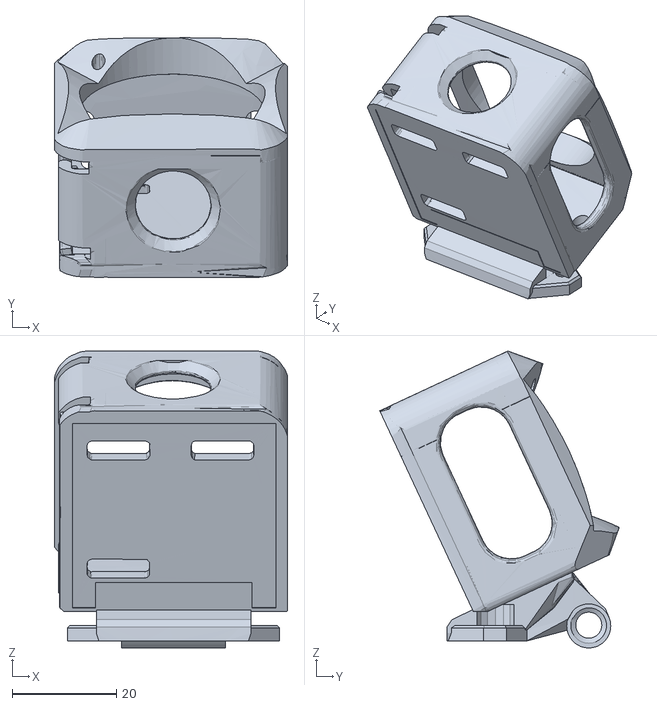
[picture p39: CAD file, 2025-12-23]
02-TPU/JeNo5_1.5+_Action2_25deg_No ND.stl
44.8 x 46.0 x 57.0

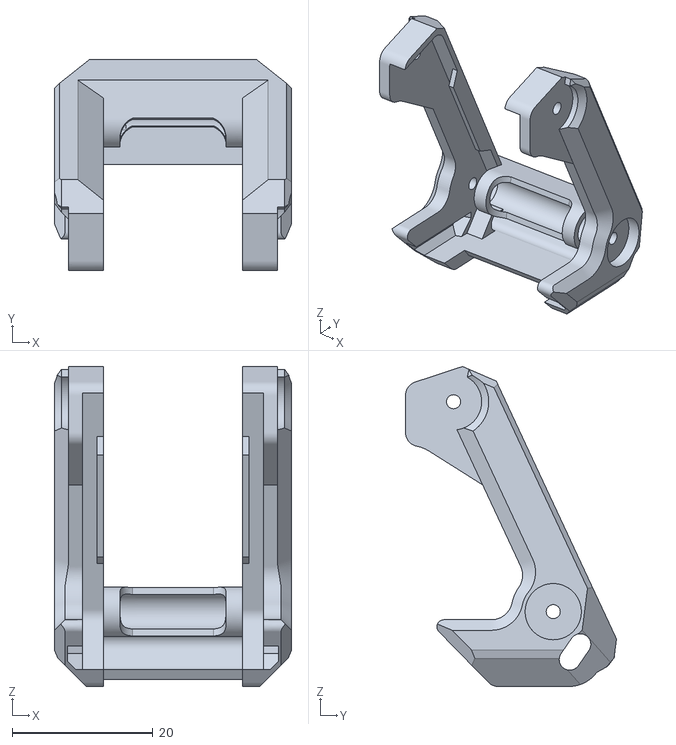
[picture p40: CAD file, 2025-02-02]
04-TPU-HISTORY/JeNo5_1.5.1_Bumper_Front_Classic_25_Bottom3mm.stl
33.8 x 30.0 x 45.5

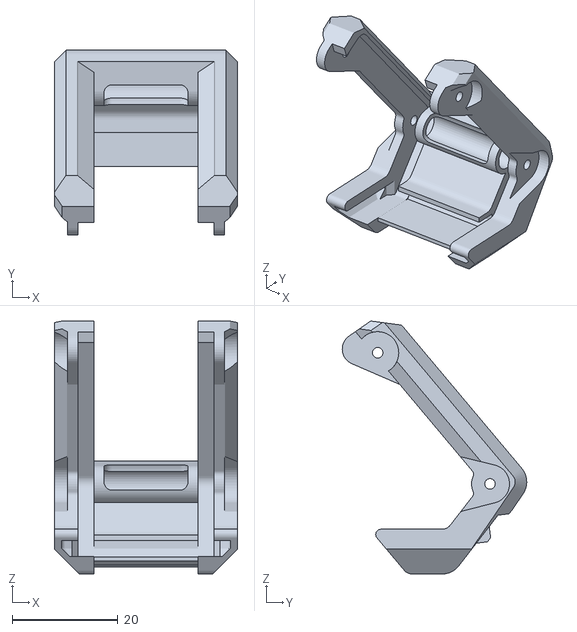
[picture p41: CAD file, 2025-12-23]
02-TPU/JeNo5_1.6_Bumper_Front_High_Tilt_40deg_3mm.stl
34.8 x 35.0 x 47.9

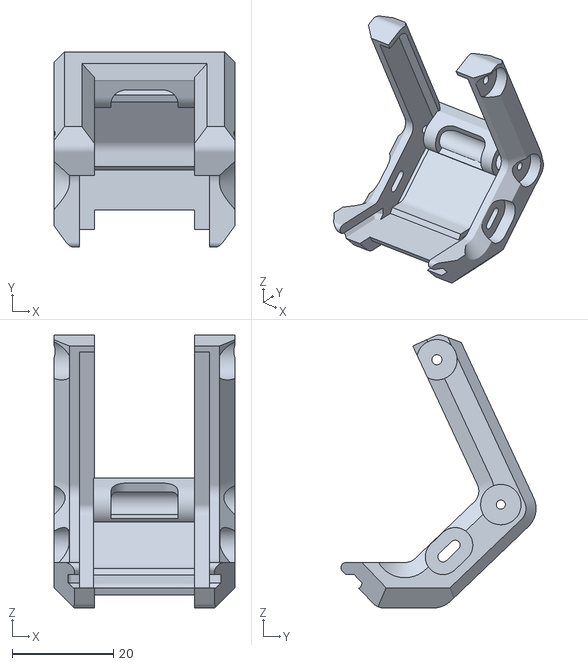
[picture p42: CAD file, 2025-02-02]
04-TPU-HISTORY/JeNo5_1.5.1_Bumper_Front_Cine_25.stl.stl
35.8 x 38.6 x 54.0

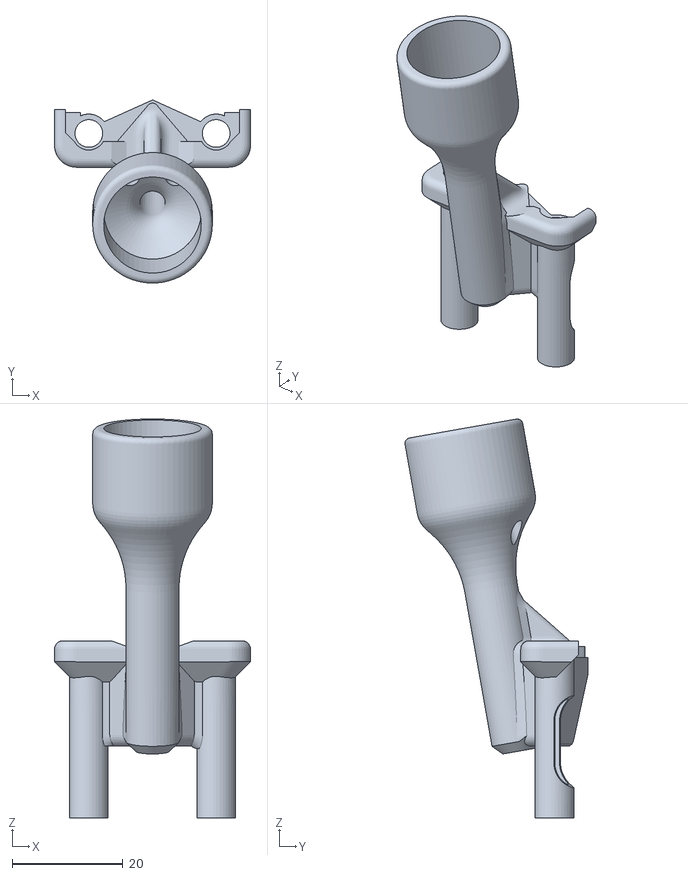
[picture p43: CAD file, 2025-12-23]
02-TPU/JeNo5_1.6_O3_Antenna_Support.stl
35.4 x 33.1 x 72.1

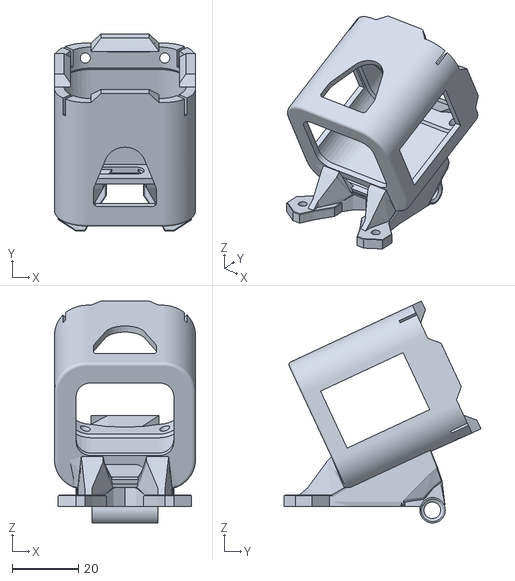
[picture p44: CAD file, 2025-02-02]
04-TPU-HISTORY/JeNo5_1.4_Session5_25deg.stl
42.6 x 59.5 x 67.1

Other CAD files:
03-FRAME-HISTORY/JeNo5_1.4.0_ALL_VERSIONS.dxf
01-FRAME/JeNo 5_1.6.0_ALL_VERSIONS.dxf
02-TPU/JeNo5_1.5+_Support_Osmo_Nano_40deg.stl
02-TPU/JeNo5_1.6_Bumper_Front_Cine.stl
04-TPU-HISTORY/JeNo5_1.5.1_Antennas_DoubleLinear.stl
01-FRAME/JeNo 5_1.6.0.stl
02-TPU/JeNo 5_1.x_Bando Arm_Socket.stl
02-TPU/JeNo5_1.5+_Action2_25deg.stl
02-TPU/JeNo5_1.5+_Action2_Mount_40deg.stl
02-TPU/JeNo5_1.5+_Bumper_Back.stl
02-TPU/JeNo5_1.5+_Bumper_Back_Bottom3mm.stl
02-TPU/JeNo5_1.5+_Softmount_O4_O3.stl
02-TPU/JeNo5_1.5+_Support_Osmo_Nano_25deg.stl
02-TPU/JeNo5_1.6_Bumper_Front_25deg.stl
02-TPU/JeNo5_1.6_Bumper_Front_Cine_3mm.stl
02-TPU/JeNo5_1.6_Bumper_Front_High_Tilt_40deg.stl
02-TPU/JeNo5_1.6_O4_PRO_Antenna_Support.stl
02-TPU/JeNo5_1.x_Antenna_DJI.stl
02-TPU/JeNo5_1.x_Arm_Classic.stl
02-TPU/JeNo5_1.x_Arm_Modus.stl
02-TPU/JeNo5_1.x_BackPack_Antenna_DJI_TAntenna.stl
02-TPU/JeNo5_1.x_BackPack_Antenna_SMA_T.stl
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

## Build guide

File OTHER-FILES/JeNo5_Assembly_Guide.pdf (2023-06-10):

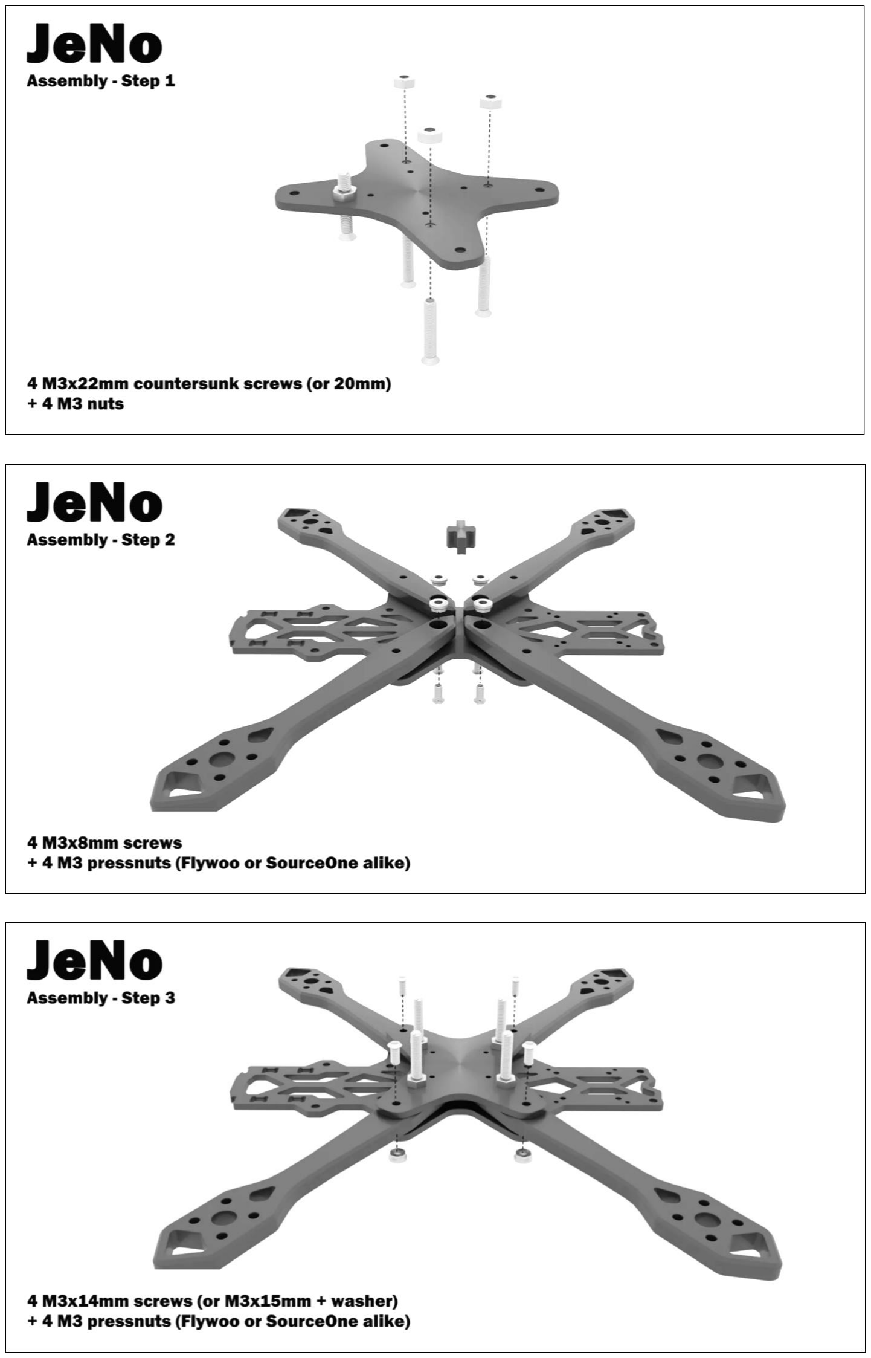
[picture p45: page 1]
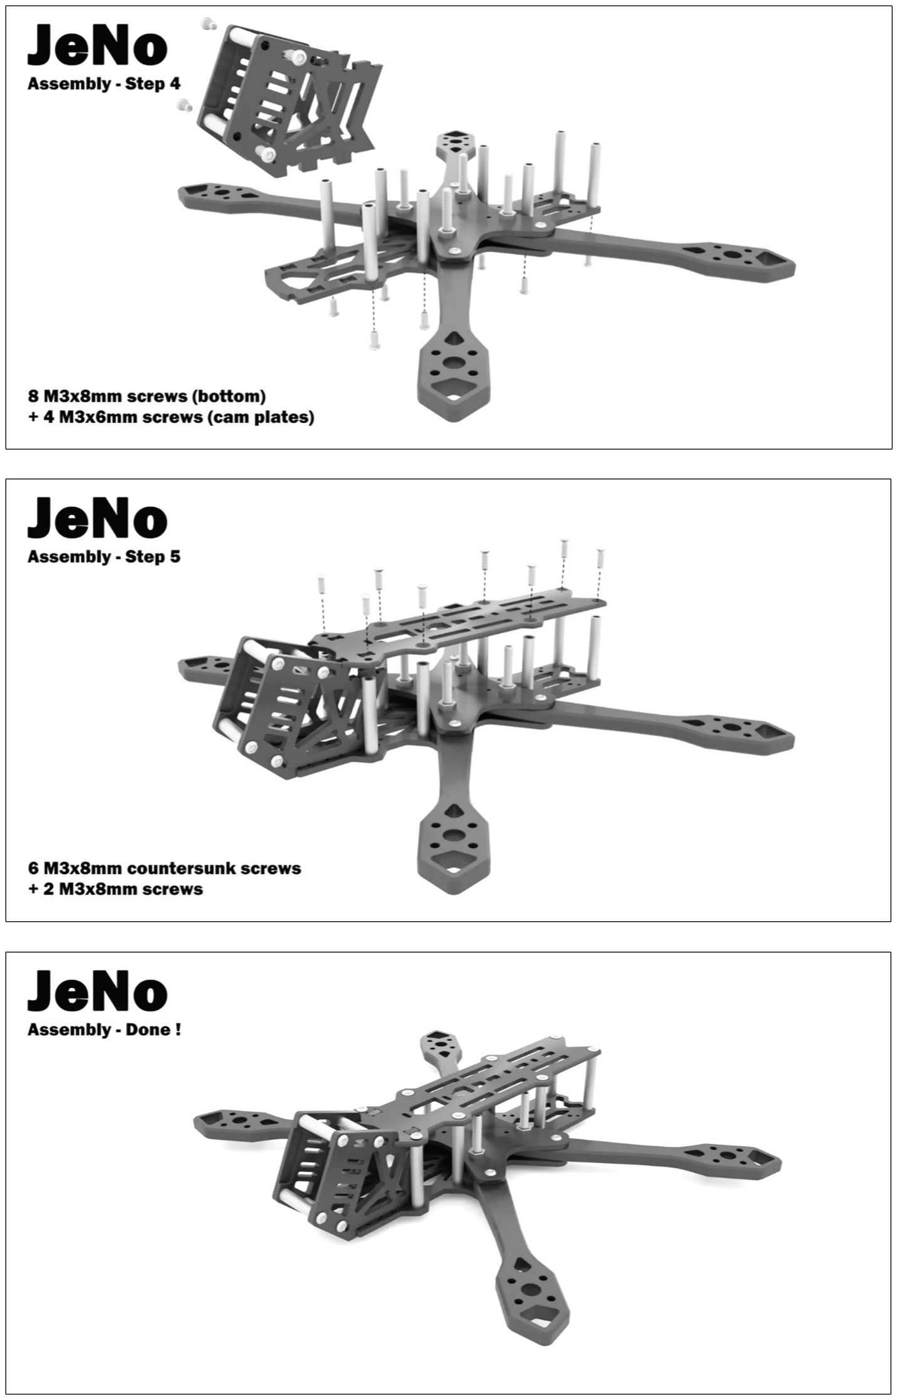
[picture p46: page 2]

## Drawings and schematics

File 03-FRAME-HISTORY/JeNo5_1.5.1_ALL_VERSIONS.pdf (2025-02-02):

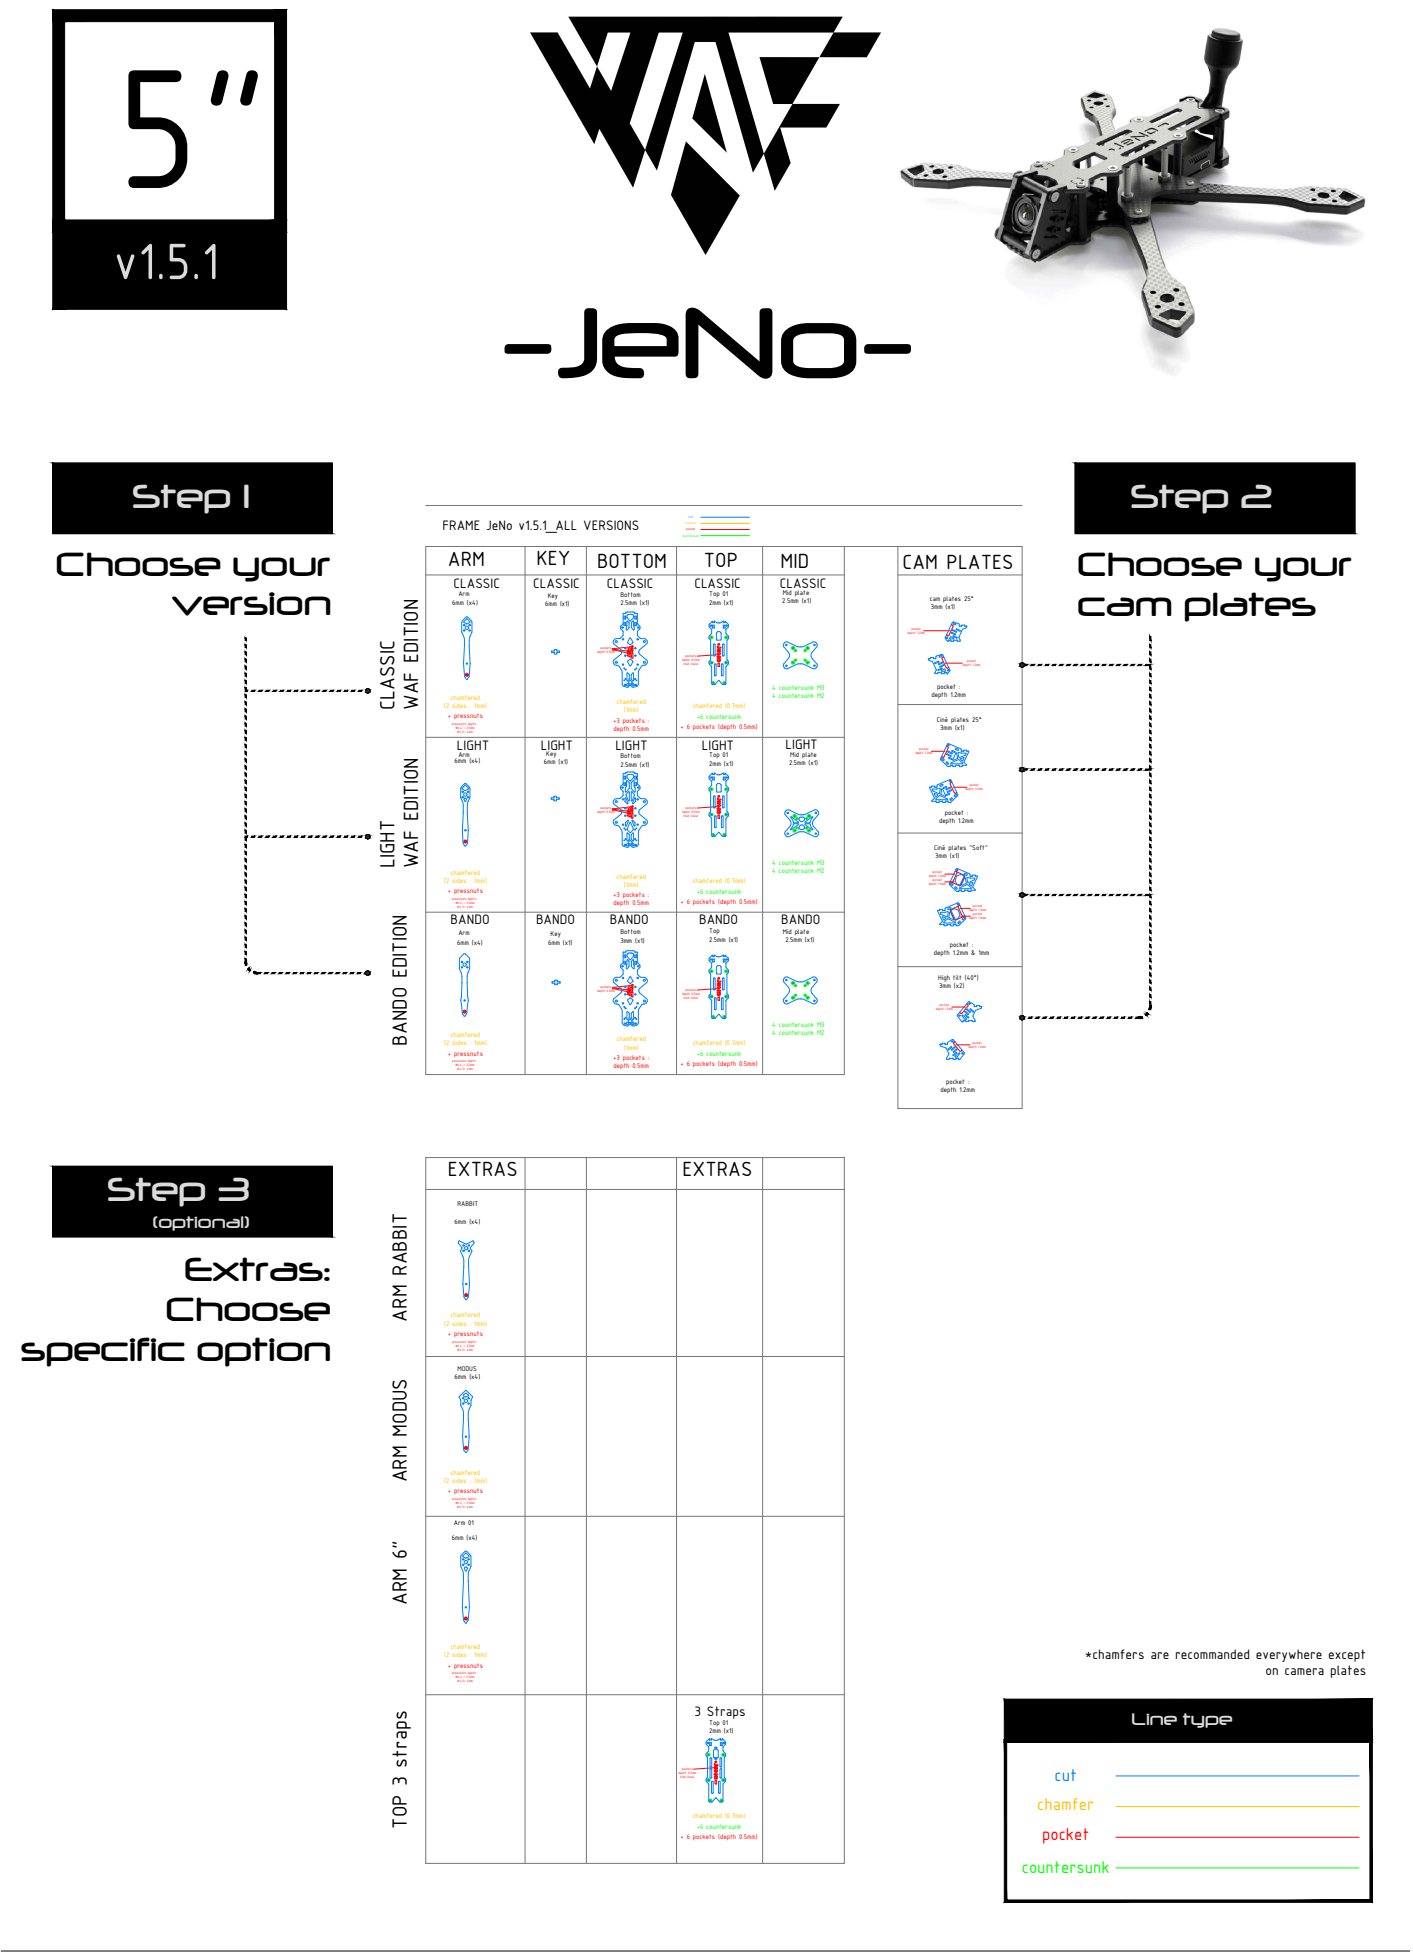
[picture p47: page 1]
+6 countersunk; depth 0.5mm; Ciné plates 25°; pocket : depth 1.2mm; chamfer pocket; High tilt (40°); pocket depth 1.2mm; pocket depth 1.0mm; depth 1.2mm & 1mm; depth 0.5mmLIGHT; LIGHT; Top 01; (red lines) BANDO EDITION; depth 0.5mm (red lines); Mid plate; chamfered (0.7mm); + 6 pockets (depth 0.5mm); (2 sides : 1mm); 4 countersunk M3 4 countersunk M2; pressnuts depth : ∅6.4 = 2.5mm; chamfered; + pressnuts; +6 countersunk +3 pockets :; Choose your; Choose your cam plates; specific option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

FRAME JeNo v1.5.1_ALL VERSIONS

ARM | KEY | BOTTOM | TOP | MID | CAM PLATES

CLASSIC Arm 6mm (x4) BANDO CLASSIC WAF EDITION LIGHT WAF EDITION ∅4.3= 4mm chamfered (2 sides : 1mm) + pressnuts pressnuts depth : ∅6.4 = 2.5mm | CLASSIC Key 6mm (x1) 6mm (x1) | CLASSIC Bottom 2.5mm (x1) pockets depth 0.5mm chamfered (1mm) +3 pockets : depth 0.5mm | CLASSIC Top 01 2mm (x1) (red lines) | CLASSIC Mid plate 2.5mm (x1) 4 countersunk M3 4 countersunk M2 | cam plates 25° 3mm (x1) pocket depth 1.2mm pocket depth 1.2mm 3mm (x1) pocket : depth 1.2mm

Ciné plates "Soft"

pocket depth 1.0mm pocket :

EXTRAS | EXTRAS

RABBIT MODUS ARM RABBIT ARM MODUS 6mm (x4) chamfered (2 sides : 1mm) ∅4.3= 4mm + pressnuts pressnuts depth : ∅6.4 = 2.5mm

6mm (x4) chamfered (2 sides : 1mm) ∅4.3= 4mm + pressnuts pressnuts depth : ∅6.4 = 2.5mm

Arm 01 ARM 6" 6mm (x4) chamfered (2 sides : 1mm) ∅4.3= 4mm + pressnuts pressnuts depth : ∅6.4 = 2.5mm

*chamfers are recommanded everywhere except

on camera plates

3 Straps (red lines) TOP 3 straps +6 countersunk Top 01 2mm (x1) chamfered (0.7mm) + 6 pockets (depth 0.5mm)

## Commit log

2023-06-10 images + assembly pdf
2023-06-12 Adding DXF and 3D Files
    [01-JeNo_Base_Classic.dxf, 01-JeNo_Base_Classic_WAF_Edition.dxf, 01-JeNo_Base_Light.dxf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]
2023-06-12 Rename DXF
    [02-JeNo_Camera_Plates_Cine_Light.dxf, 02-JeNo_Camera_Plates_Cine_Soft.dxf]
2023-06-25 Adding camera mounts
    [JeNo_GoPro_6_7_25deg.stl, JeNo_GoPro_9_10_11_WaF_25deg.stl, JeNo_Session5_40deg.stl]
2023-09-08 Adds TPU set for bando
    [JeNo_DJI_Action2_Bando_20deg.stl, JeNo_DJI_Action2_Bando_25deg.stl, JeNo_VTX_Cherry_Antenna_Support_bando.stl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]
2023-09-16 Update JeNo_arm protect_full_socket_bando.stl
    [JeNo_arm protect_full_socket_bando.stl]
2023-09-18 Added cine front bumper + bando TPU set pic
    [JeNo_front_bumper_cine_bando.stl]
2024-04-25 Reporting updates from printables
    [03-JeNo_Arm classic_bando_edition.dxf, JeNo_3D_v1.21.step, JeNo_3D_v1.21.stl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]
2024-04-29 arms update
    [03-JeNo_Arm_Classic.dxf, 03-JeNo_Arm_Rabbit.dxf]
2024-07-28 New Action2 Mount for bando
2024-10-01 fix JeNo_arm protect_full_socket_bando.stl
    [JeNo_arm protect_full_socket_bando.stl]
2025-02-02 Version 1.5.1 : O4 Pro compatibility
    [01-JeNo_Base_Classic.dxf, 01-JeNo_Base_Classic_WAF_Edition.dxf, 01-JeNo_Base_Light.dxf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]
2025-02-09 new cam plates
2025-02-16 tpu for softmounted cam plates
    [JeNo5_Softmount_O4_O3.stl]
2025-09-02 Apply line ending normalization for DXF
    [JeNo5_ALL_VERSIONS_1.4.0.dxf, JeNo5_ALL_VERSIONS_1.5.1.dxf]
2025-09-17 New bando TPU for arms and motors
    [JeNo5_Bando-Arm_Screws_Skate.stl, JeNo5_Bando_Arm_Screws.stl, JeNo5_Bando_Arm_Socket.stl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]
2025-09-17 rename file
    [JeNo5_Bando_Arm_Screws_Skate.stl]

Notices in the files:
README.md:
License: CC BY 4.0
